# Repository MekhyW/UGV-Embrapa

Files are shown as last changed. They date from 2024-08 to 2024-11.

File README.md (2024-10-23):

# UGV-Embrapa: Unmanned Ground Vehicle for Agricultural Monitoring

Embrapa Logo Insper Logo NASA OSR Logo

## Useful Links

- [Project Documentation](https://mekhyw.github.io/UGV-Embrapa/)
- [First Project Paper (robot platform)](paper-1.pdf)
- [Second Project Paper (autonomous SLAM/navigation module)](paper-2.pdf)
- [Mentor's Projects](https://www.embrapa.br/equipe/-/empregado/351534/thiago-teixeira-santos)
- [NASA JPL Open Source Rover](https://jplopensourcerover.com/)

## What is this project?

This project aims to develop an Unmanned Ground Vehicle (UGV) for monitoring fruit and forestry plots, inspired by NASA's Open Source Rover project. The UGV is designed to navigate autonomously and safely between rows of agricultural fields, providing valuable data for research and management.

## Context

This UGV was developed by students of Insper College as part of their Capstone Engineering Project, in collaboration with Embrapa (Brazilian Agricultural Research Corporation), during the first and second semesters of 2024. The project builds upon the foundation laid by the NASA JPL Open Source Rover, adapting it for agricultural applications.

## Directory Structure

```
UGV-Embrapa/
├── .github/
│   └── workflows/
├── docs/
├── Electronics/
├── Mechanics/
├── Software/
├── README.md
└── ugv-embrapa.pdf
```

## Contributors

- Breno Alencar Araújo
- Bruno Morales Balkins
- Fernando Bichuette Assumpção
- Giulia Carolina Martins de Sampaio
- Felipe Catapano Emrich Melo
- Rafael Eli Katri
- Gabriel Brunoro Motta Tumang
- Luana de Matos Sorpreso

Advisor: Prof. Dr. Vinícius Licks
Mentor: Thiago Teixeira Santos

For detailed information about the project, including setup instructions, technical details, and results, please refer to the [project documentation](https://mekhyw.github.io/UGV-Embrapa/).

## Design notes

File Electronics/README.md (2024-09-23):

# Electronics 

## Schematics and General Operation Details 

The prototype's electronics are composed of two boards: the motor drive board (Motor Board), where the power circuits are located, and the board responsible for controlling the entire system's operation (Brain Board), where the control circuits are located and a Raspberry Pi 4, model B, 8 GB, with a 64-bit quad-core ARM-Cortex A72 microprocessor, running at 1.5 GHz, is located.



### Power Supply Diagrams

First, analyzing the system power supply, a battery supplying 14.8V DC is connected directly to the drive board, passing through a protection circuit, which has a fuse, a 1 kΩ resistor and a diode, which act as protection for the motor circuit. In addition, a voltage and current monitoring module (INA260) is used to measure overcurrent, in addition to a multimeter, which is used for user monitoring of current and voltage data.



The 14.8V voltage is used to power two regulators, a 12V step-down regulator (D24V22Fx), used to power the Roboclaw drivers, and a 5V regulator (D24V150Fx). There is also a third voltage regulator that converts the voltage from 5V to 3.3V (MIC2937A-3.3WT), powering the PWM expansion module (PCA9685), the voltage and current monitor, and the signaling LEDs on both boards. The 5V voltage, in turn, also powers the PWM expansion module, the servos, the Raspberry Pi, the HMI display, and the motor encoders. The motors are powered by Roboclaw via PWM with a maximum voltage of 12V.

### Signal Diagrams

For the system signal diagram, note that a new block has been added, the set between the operator and the radio control, responsible for sending commands via radio waves to the Raspberry Pi, which receives the signal via a USB module. The data received by the microprocessor is sent via serial and used to control the motors and servos.



The control loop for the six motors is controlled by the Raspberry Pi, which receives the reference from the radio control and sends the commands to the Roboclaw drivers, which perform the activation via PWM. The loop is closed by the encoders, which are responsible for the sensing, sending the collected data to the controller present in the driver.

The four servos, in turn, are controlled in an open loop (internally closed) activated by means of a PWM signal. This signal is provided by the PCA9685 module (expansion), used to increase the number of servos that can be controlled, by generating 16 new PWM channels. Communication between this module and the Raspberry Pi occurs via the I2C communication protocol.

Considering the communication between the microcomputer and the voltage and current monitoring module (INA260), it is noted that data is also sent via an I2C communication protocol. The module also communicates with the signaling LEDs to alert the user if its internal shunt resistor detects any change in the power supply system.

In addition to the expansion module and the monitor, communication with the HMI display, which will be implemented in the future, will also occur according to the I2C protocol. The reason for this choice is that the control board has an available I2C bus, which could be adapted for connecting the display with a low number of necessary adaptations.

Another important observation regarding the diagram is that the Raspberry Pi is also responsible for controlling the 12V voltage regulator through an enable signal, turning the 12V output on or off.

A closer look at the control board reveals the presence of some signaling LEDs. These components are intended for communication with the user, signaling, for example, when data is being transferred via the serial port, lighting up when the bits are transferred.

Finally, the last data stream to be analyzed is the emergency status indicator, in which a high logic level digital signal is sent by the emergency button to the microprocessor, which communicates the situation to the user via the HMI display.

## Physical Emergency Circuit

The schematic of the physical emergency circuit used to de-energize the robot is illustrated below.



To indicate the emergency status to the user, a red indicator light was adopted, which lights up as soon as the button is pressed. The component has an internal resistance of 1800 Ω, supporting voltages of up to 24V and is activated by a normally open switch, responsible for closing the circuit after the button is pressed.

A remote emergency button was also implemented, whose operation is explained in the programming folder.

## Display Circuit Details

The schematic of the display pin connection to ensure I2C communication is shown below. The pins for connecting 5V and GND are available on the Raspberry Pi and an extension of the SCL and SDA pins can be found on the control board.



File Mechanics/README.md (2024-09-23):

# Mechanics

## 3D Model
The base 3D model can be found in [OnShape](https://cad.onshape.com/documents/e4f00b1a3d2edb1a84bbba1c/w/8ab8f394324bcc586236ef5d/e/9191e5ad2a70f387b419bc55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) or in the STEP file provided above.



## Adaptations to Official Documentation
Some adaptations were necessary in the assembly of the official documentation, since the components were imported and some of them were not available for delivery. To get around this problem, equivalent parts were purchased that would allow adaptation for the proposed application.
The parts that underwent this adaptation process are listed and commented below.
### Suspension Profiles
The first parts to be adapted were the aluminum profiles that make up part of the robot's suspension, since it was not possible to find them in the lengths specified in NASA's official documentation, 96 mm. As an alternative, larger profiles were purchased and cut to the correct size.



After cutting the profiles, the thread for the M4 screw used in the assembly had to be redone for all four holes in each of the cut parts. The threading operation was carried out manually and consisted of three stages, using taps of different sizes until the desired thread size was reached. The part did not need to be drilled again, since its holes were through holes, covering the entire structure, regardless of length.



### Aluminum Body Bars

The aluminum bars used to assemble the robot body also needed to be adapted, since they were also purchased in a length greater than that specified and then cut to the correct size, 96 mm.

After performing the cutting operations on the parts, it was necessary to drill the bars, since the existing hole was not through like in the profile. In addition, it was also necessary to perform the threading in two stages, as was the case with the other part mentioned above.

During the drilling operation, the following steps were performed to ensure better alignment of the hole:

1. Painting the face to be drilled with a marker.

2. Removing the paint to mark the hole with the aid of a vertical height marker. The line was drawn with a dimension equivalent to half the side of the face, ensuring that the straight lines intersect in the center.

3. Making a central mark to ensure that the drill is not inserted misaligned, a step performed with a center punch, a vice and a hammer.

4. Drilling with the aid of a manual benchtop milling machine, aiming to align the tip of the drill with the marking made in the previous step. Advance and retreat the drill during the process, ensuring chip evacuation and dissipation of the heat generated.



The threading process was also necessary and was redone in a manner identical to the procedure described for the profiles.

The part with the bearing for fitting the suspension was also not available in the original model in NASA documentation, so another with an equivalent internal diameter was used (Figure 28). Although the replacement did not fit perfectly and caused slight structural deformation, it was decided not to make any adaptations because the components could be damaged and there were no substitutes. The resulting deformation effect did not compromise the rover's operation.



## Review of Official Documentation Errors

One of the suspension components was incorrectly identified in the official documentation, with initial code 1601, which in reality corresponds to component number 1611. In the 3D view of the assembly, the part identified with the code corresponding to that informed in the official documentation has an internal diameter with a value of less than 8 mm, not assembling on the specified axle.



## Additional Components Manufactured

To ensure the robot's adaptability to the monitoring environment, some additional components needed to be manufactured, including the camera and LiDAR supports, allowing these components to be placed in the structure in the future.

### Camera Support

As requested by the client, some supports for cameras and a LIDAR were also developed, using Fusion 360 software for modeling and 3D printing technology to materialize the project.

suporte1

Screenshot at Jun 10 11-16-50

### LiDAR Support

suporte3

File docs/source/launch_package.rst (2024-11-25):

Launch Package
===============

The osr_autonomous package contains the launch files for the robot, for operation using the SLAM and navigation stack described in previous sections (for the Raspberry Pi's launch package, refer to the Raspberry Pi's environment setup section).

Usage
-----

1) First, make sure the package is built and sourced in your ROS 2 workspace:

   .. code-block:: bash

      cd UGV-Embrapa/Software/osr_autonomous
      colcon build --packages-select osr_autonomous
      source install/setup.bash

   .. note::
      You can also source the ROS 2 environment from the Environment Setup - Dell Optiplex section. Refer to it for more information.

2) Then you can launch any of the files using the ros2 launch command with the package name and launch file name:

   .. code-block:: bash

      ros2 launch osr_autonomous gps_launch.py

      ros2 launch osr_autonomous ir_depth_launch.py

      ros2 launch osr_autonomous rosbag_launch.py

      ros2 launch osr_autonomous rtab_imu_launch.py

      ros2 launch osr_autonomous stereo_launch.py

3) For the rosbag_launch.py, you can specify a custom directory for saving the bag files:

   .. code-block:: bash

      ros2 launch osr_autonomous rosbag_launch.py bag_dir:=/path/to/save/bags

   .. note::

      Also, ensure that:

      - Your RealSense D435i camera is properly connected
      - If using GPS features, your GPS device is connected and configured
      - The robot's URDF is properly set up in the osr_gazebo package
      - Parameter files exist in the correct locations:
         - ``osr_autonomous/realsense_params/params.yaml``
         - ``osr_autonomous/nav2_params/params.yaml``
         - ``osr_autonomous/nav2_params/map.yaml``

Configuration Notes
--------------------

   - All launch files support parameter overrides via command line arguments
   - RTAB-Map parameters are optimized for real-time performance
   - Transform configurations assume standard sensor mounting positions
   - Nav2 parameters and maps are loaded from the osr_autonomous package

Launch Files
------------

The launch files are designed to support different operational modes and sensor configurations for the UGV. Each launch file serves a specific purpose in the robot's operation, from basic visual SLAM to full GPS-aided navigation.

gps_launch.py
^^^^^^^^^^^^^

This launch file implements a complete navigation stack with GPS integration. It's ideal for outdoor operations where GPS signals are available.

Key Features:

   - Initializes RealSense D435i camera in IR/depth mode
   - Enables IMU (gyroscope and accelerometer)
   - Sets up RTAB-Map for visual SLAM
   - Configures Nav2 for autonomous navigation
   - Integrates GPS data via the NMEA driver
   - Uses robot_localization for sensor fusion
   - Includes GPS waypoint following capability

ir_depth_launch.py
^^^^^^^^^^^^^^^^^^

A simplified version focused on indoor navigation using IR and depth data from the RealSense camera.

Key Features:

   - Configures RealSense D435i for IR and depth streaming
   - Sets up RTAB-Map for visual SLAM
   - Enables Nav2 for autonomous navigation
   - Uses IMU data for improved odometry
   - Excludes GPS-related components

rosbag_launch.py
^^^^^^^^^^^^^^^^

Similar to gps_launch.py but includes ROS bag recording functionality for data collection and post-processing.

Key Features:

   - Includes all functionality from gps_launch.py
   - Adds automatic ROS bag recording of all topics
   - Configurable output directory for recorded bags
   - Useful for development and debugging

lidar_launch.py
^^^^^^^^^^^^^^^

Similar to gps_launch.py but with LiDAR integration for improved mapping and navigation (complete stack without bag recording).

Key Features:

   - Includes all functionality from gps_launch.py
   - Adds LiDAR data integration
   - Improved mapping and navigation capabilities
   - No ROS bag recording

rtab_imu_launch.py
^^^^^^^^^^^^^^^^^^

Specialized configuration focusing on RGB-D SLAM with heavy IMU integration.

Key Features:

   - Uses RGB color stream instead of IR
   - Enhanced IMU integration with RTAB-Map
   - Configured for improved 3D mapping
   - Forces 2D constraints for better ground robot operation
   - More aggressive feature detection settings

stereo_launch.py
^^^^^^^^^^^^^^^^^

Basic stereo vision configuration using the RealSense camera's IR sensors.

Key Features:

   - Minimal configuration using IR and depth
   - No IMU integration
   - Basic RTAB-Map configuration
   - Lighter weight than other launches
   - No navigation stack integration

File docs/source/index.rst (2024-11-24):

.. UGV Embrapa documentation master file, created by
   sphinx-quickstart on Tue Oct 15 21:59:05 2024.
   You can adapt this file completely to your liking, but it should at least
   contain the root `toctree` directive.

UGV-Embrapa: Unmanned Ground Vehicle for Agricultural Monitoring
================================================================

Welcome to the documentation for the UGV-Embrapa project, an Unmanned Ground Vehicle (UGV) for monitoring fruit and forestry plots. 
Here you will find information about the project, how to assemble and use the robot and how to setup the software stack to perform autonomous navigation, mapping and telemetry.

.. toctree::
   :maxdepth: 2
   :caption: Contents:

   papers
   overview
   mechanical_assembly
   schematics_and_wiring
   environment_setup_rpi
   remote_control
   environment_setup_optiplex
   launch_package
   waypoint_navigation
   cloud_architecture
   contributors

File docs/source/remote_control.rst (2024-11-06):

Remote Control Operation
========================

The UGV (Unmanned Ground Vehicle) can be operated manually using a Spektrum DXS radio control transmitter, which communicates with a receiver installed in the UGV. This section describes how to use the remote control for manual operation of the robot.

Controller Setup
----------------

The mapping of control buttons and levers has been configured to facilitate the operation of the UGV. The following parameters have been set for the controller:

- **scale_linear.x**: 0.12
- **axis_linear.x**: 1
- **axis_angular.yaw**: 2
- **axis_angular.pitch**: 4
- **scale_angular.yaw**: 1.25
- **scale_angular.pitch**: 0.25
- **scale_angular_turbo.yaw**: 0.0
- **scale_linear_turbo.x**: 0.0
- **enable_button**: 0
- **enable_turbo_button**: 1

These parameters are used by the ROS 2 `joy` node to interpret the controller inputs.

Control Mapping
---------------

1. **Speed Control**:
   The left lever controls the speed of the UGV. Push forward to move the UGV forward, and pull back to reverse.

2. **Direction Control**:
   The right lever is responsible for steering the UGV. Move the lever left or right to rotate the UGV in the respective direction.

3. **On/Off Switch**:
   The lower central button turns the UGV on or off.

4. **Emergency Stop**:
   The emergency button is located at the top left of the controller. When pressed, it immediately stops the UGV by setting `scale_linear_turbo` to 0.0.

5. **Fine Rotation**:
   A switch at the top right of the controller allows for fine adjustment of rotation.

6. **Deadman Switch**:
   Located on the back of the controller, this button must be continuously pressed to keep the UGV operational. Releasing it will immediately stop the UGV as a safety measure.

Emergency Routine
-----------------

An emergency routine has been implemented to ensure the operational safety of the rover:

1. When the emergency button is pressed, `scale_linear_turbo` is set to 0.0.
2. This results in the rover coming to a complete and immediate stop.

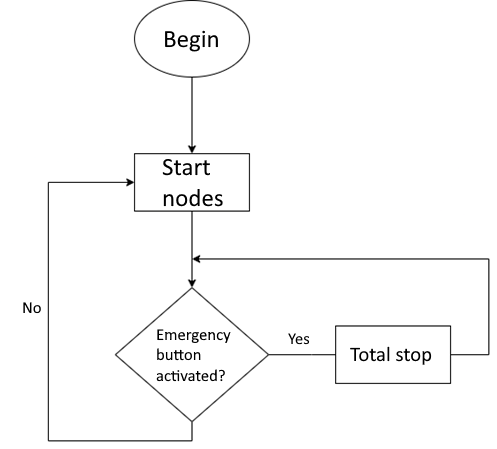
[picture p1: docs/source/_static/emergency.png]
Emergency flowchart


Operating the UGV
-----------------

1. Ensure the receiver dongle is properly connected to the UGV.
2. Turn on the Spektrum DXS radio control transmitter.
3. Use the On/Off switch to power up the UGV.
4. Press and hold the Deadman switch on the back of the controller.
5. Use the left lever to control speed and the right lever to steer.
6. For fine rotations, use the rotation switch at the top right.
7. In case of emergency, press the emergency stop button to immediately halt the UGV.
8. When finished, use the On/Off switch to power down the UGV.

.. note::
   Remember to always operate the UGV in a safe environment and follow all safety protocols.

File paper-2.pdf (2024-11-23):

Veículo Terrestre Autônomo para Monitoramento de Talhões de Silvicultura e Plantações de Frutas

Felipe Catapano Emrich Melo Gabriel Brunoro Motta Tumang Luana de Matos Sorpreso
Rafael Eli Katri

Trabalho de Conclusão de Curso

Relatório do Projeto Final - Capstone

São Paulo - SP – Brasil
Agosto 2024

Felipe Catapano Emrich Melo Gabriel Brunoro Motta Tumang Luana de Matos Sorpreso
Rafael Eli Katri

Veículo Terrestre Autônomo para Monitoramento de Talhões de Silvicultura e Plantações de Frutas

Trabalho de Conclusão de Curso

Relatório do Projeto Final - Capstone

Relatório apresentado aos respectivos cursos de Graduação em

Engenharia | (Computação/Mecânica/Mecatrônica), | como

requisito parcial para a obtenção do título de Bacharel no

respectivo curso.

Professor Orientador: Prof. Dr. Vinicius Licks

Mentor: Thiago Teixeira Santos

Coordenador TCC/Capstone: Prof. Dr. Luciano Pereira Soares

São Paulo - SP – Brasil
Agosto 2024

Felipe Catapano Emrich Melo Gabriel Brunoro Motta Tumang Luana de Matos Sorpreso
Rafael Eli Katri

Veículo Terrestre Autônomo para Monitoramento de Talhões de Silvicultura e Plantações de Frutas

Relatório apresentado aos respectivos cursos de Graduação em

Engenharia | (Computação/Mecânica/Mecatrônica), | como

requisito parcial para a obtenção do título de Bacharel no

respectivo curso.

Professor Orientador: Prof. Dr. Vinicius Licks

Banca Examinadora

Prof. Dr. Vinicius Licks

Insper

Prof. Dr. Fabio Ferraz Junior

Insper

Prof. Dr. Fabricio Jailson Barth

Insper

Prof. Me. Fabio Roberto de Miranda

Insper

RESUMO

Este projeto visa desenvolver um sistema de navegação autônoma para um robô de

monitoramento de silvicultura e pomares montado pela iteração anterior deste Capstone. O

projeto tem como propósito automatizar o processo de monitoramento de tais plantações,

possibilitando a otimização da mão de obra humana. O programa para esta funcionalidade nova

será desenvolvido utilizando o framework ROS 2, e mais especificamente o pacote de

navegação NAV 2. Para conseguir atingir o objetivo final, foi estudado pelo grupo múltiplas

soluções e algoritmos de SLAM (Simultaneous Localization and Mapping) compatíveis com

fusão de sensores de múltiplos tipos, para mapeamento multissensorial robusto em ambientes

não estruturados com terreno irregular. Para achar a solução ideal para os requisitos de projeto,

foi adotado a ferramenta da matriz de soluções.

Palavras-chave: Navegação Autônoma; Monitoramento de plantações; SLAM; ROS 2; NAV

2; UGV;

ABSTRACT

This project aims to develop an autonomous navigation system for a forestry and orchard

monitoring robot assembled by the previous iteration of this Capstone. The project aims to

automate the monitoring process of such plantations, enabling the optimization of human

labor. The program for this new functionality will be developed using the ROS 2 framework,

and more specifically the NAV 2 navigation package. To achieve the final objective, the

group studied multiple solutions and SLAM algorithms compatible with sensor fusion of

multiple types, for robust multisensory mapping in unstructured environments with uneven

terrain. To find the ideal solution for the project requirements, the solution matrix tool was

adopted.

Keywords: Autonomous Navigation; Plantation Monitoring; SLAM; ROS 2; NAV 2; UGV.

3.4 | ESCOLHA DE SISTEMA OPERACIONAL E DISTRIBUIÇÃO DE ROS PARA O MÓDULO DE NAVEGAÇÃO ..... 35

### 1 Introdução

1.1 Proposta do projeto

O objetivo do projeto é a implementação de um sistema de navegação autônoma e de

monitoramento de trajetória para um UGV (Unmanned Ground Vehicle), ou seja, um veículo

terrestre não tripulado. O veículo deve ser capaz de planejar seu movimento e enviar

informações de posicionamento enquanto navega por corredores de talhões, a unidade básica

de plantio agrícola. A iteração atual faz parte de um contexto maior de projetos de UGV’s para

uso agrícola, representando continuidade ao Capstone anterior responsável pela montagem do robô a ser utilizado, capaz de atuar em pomares e talhões de silvicultura (ARAÚJO et al, 2024).

Diferentemente da iteração passada, o UGV não é operado manualmente com um

controle remoto. O robô deverá, com o auxílio de uma ferramenta de software interativa,

receber um conjunto de pontos chamados de waypoints e, sem comandos adicionais do

operador, ser capaz de navegar de ponto a ponto autonomamente. Para isso, foi desenvolvido

um módulo separado de navegação autônoma, composto por um conjunto de sensores e uma

unidade computacional dedicada, que deverá processar tarefas de localização, mapeamento e

navegação e se comunicar com o serviço de atuação dos motores do módulo base do UGV. Isso

se deve principalmente pelo caráter crítico da atuação dos motores do veículo, que não deve ser

comprometido pelos processos alto nível da navegação autônoma.

A navegação autônoma e o acompanhamento do percurso via interface interativa

servirão de base para aplicar futuramente técnicas de agricultura de precisão, principalmente

no que se trata de monitoramento de plantio. Esse caso de uso traz valor para o agronegócio

dado que pode ser usado para controle de pragas e planejamento de plantações. Esse tipo de

monitoramento poderá ser explorado em futuras iterações, que beneficiam da navegação do

robô pelos talhões e a publicação de informações de telemetria que informam o seu

posicionamento.

O UGV, desde a iteração anterior, utiliza o ROS (Robot Operatintg System), um

framework open-source de robótica que padroniza o desenvolvimento de robôs e facilita a

colaboração entre usuários. Nesse sentido, o ROS oferece padrões de comunicação entre

sensores, atuadores e computadores, permitindo que o desenvolvedor não se preocupe com a

implementação baixo nível da transmissão de dados. Além disso, o ROS disponibiliza

ferramentas de visualização e definição de waypoints.

O framework permite que projetos sejam convertidos em pacotes que podem ser

facilmente instalados e acessados por outros desenvolvedores. Desse modo, a comunidade ROS

de robótica mantém pacotes open-source sobre as mais diversas áreas de atuação no campo de

robótica. ROS também é relevante para aplicações no mercado de trabalho, sendo que mais de

900 empresas o utilizaram em 2023, com um aumento de 22.9% em relação ao ano anterior

(SCOTT, 2024).

No que diz respeito a navegação, os pacotes ROS utilizados fazem parte da plataforma

NAV 2. Esses pacotes são desenvolvidos pela Open Navigation, uma empresa que cria soluções

open-source para tarefas de navegação. O NAV 2 é uma plataforma utilizada no mercado, sendo

usada por empresas como Toyota, LG e Bosch (NAV 2, 2024). Um grande diferencial da

plataforma é sua modularidade, sendo que é fácil customizar o comportamento de seus

planejadores, ou até mesmo criar comportamentos usando o sistema de plugins (DOCS NAV

2, 2024). Outro ponto forte é a disponibilidade de plugins prontos com algoritmos de

planejamento e suavização de rotas, árvores de comportamento, entre outros (DOCS NAV 2,

2024).

Um sistema de navegação autônoma depende de técnicas de localização e mapeamento

para obter informações do posicionamento do robô em relação a um ponto de referência (Corke,

2011, p. 125). Uma solução para isso é uso de GPS (Global Positioning System), um sistema

que estima a posição diretamente com uso de satélites. Sensores GPS-RTK são comumente

usados, oferecendo precisão na escala de centímetros. Entretanto, para o caso de uso do projeto,

no contexto da silvicultura com áreas densas de árvores, é conhecido que essas áreas sofrem de

bloqueios e reflexões de sinal (AGUIAR et al, 2020), o que gera instabilidades.

Nesse sentido, uma técnica relevante é o SLAM (Simultaneous Localization and

Mapping), que consiste na localização e mapeamento simultâneos de um ambiente não

explorado (CORKE, 2011, p. 167). Existem diversas implementações de SLAM, incluindo

SLAM baseado em LiDAR’s 3D e SLAM visual que são relevantes para ambientes externos

(FASIOLO et al, 2023). Outra questão relevante é o SLAM multi-sensor, que realiza fusão de

sensores para evitar o acúmulo de erros na coleta dos sensores, também chamado de drift

(FASIOLO et al, 2023). Isso é relevante em ambientes externos, que são sujeitos a efeitos

climáticos desfavoráveis, uma vez que as leituras de um sensor podem compensar falhas do

outro (ZHU, 2024).

Soluções de SLAM usando LiDAR 2D são conhecidas, computacionalmente eficientes

e robustas para ambientes fechados, entretanto elas não têm a mesma eficácia no contexto do

projeto como fonte única de sensoriamento (REGER, 2022) e podem assumir um papel auxiliar

na fusão de sensores. Esse auxílio pode se dar tanto no refinamento da odometria visual, quanto na otimização do mapa com a identificação de loop closures (LABBÉ, 2019).

Com essas questões em mente, propõe-se utilizar uma câmera de profundidade Intel

Realsense D435i e um LiDAR 2D Robotis LDS-02 para as tarefas de localização e

mapeamento, em conjunto com o módulo de GPS. Será utilizado o pacote ROS RTAB-MAP,

um projeto open-source da Université de Sherbrooke, que se diferencia por oferecer suporte a

uma variedade de sensores e pela possibilidade de realizar SLAM multi-sensor. A câmera

Realsense será utilizada para extrair odometria visual e coletar features usando o modo RGB-

D e o IMU interno da câmera será usado como referência para aperfeiçoar o SLAM. O LiDAR

2D também será utilizado no refinamento da odometria visual e na otimização do mapa com a

identificação de loop closures.

1.2 Origem do Desafio

Com base no relatório final do semestre passado foi pensado na origem do desafio,

considerando que o resultado de ambos os projetos é o mesmo. A Embrapa (Empresa Brasileira

de Pesquisa Agropecuária) é uma empresa que foca em pesquisa para a agropecuária no Brasil.

Se trata de uma empresa pública vinculada ao Ministério da Agricultura e Pecuária (MAPA),

criada em 1973.

O objetivo do desenvolvimento do UGV no contexto agrícola é facilitar o

monitoramento de talhões de fruticultura e silvicultura, permitindo que esse trabalho se torne

mais preciso e rápido. O talhão é uma parte do solo que representa a unidade mínima de cultivo.

A separação por talhões é de extrema relevância para a fruticultura pois permite um

controle por área da fruta, dessa forma, é possível isolar um talhão que esteja contaminado por

pragas, por exemplo. Além disso, cada talhão pode conter um tipo de fruta específico, o que faz

com que seja possível uma maior organização no plantio e na colheita.Já no caso da silvicultura,

o talhão também se mostra muito importante, uma vez que, a área florestal é dividida em

unidades territoriais de acordo com características específicas da floresta, assim cada talhão

tem o seu método silvicultural adequado.

Dessa forma, é evidente que o monitoramento dos talhões é essencial para o controle de

pragas e o planejamento de toda a produção e colheita. Por conta da grande relevância do setor agrícola no Brasil, o monitoramento de talhões realizado por seres humanos pode ser dificultado

por conta do grande número de talhões ou até mesmo sua extensão, dessa forma, a inclusão de

UGVs nessa etapa do processo produtivo pode ser de grande auxílio para a realização dessa

tarefa, além de permitir que haja um planejamento maior sobre aquela área.

Atualmente, existem algumas maneiras distintas de realizar o monitoramento, nenhuma

delas tão automatizada quando o UGV. No caso do monitoramento de pragas do mamão em

2018, foi feito um aplicativo móvel onde o produtor preenche planilhas com informações

relevantes como insetos encontrados e quantidade de frutos. Com isso o aplicativo pode

recomendar a pulverização da plantação, além das informações em tempo real disponibilizadas

pelo aplicativo (RODRIGUES et al, 2018).

Essa tecnología, apesar de ainda se mostrar menos automatizada que o UGV, onde não é

necessário que um operador preencha uma planilha, já que o robô já analisa os dados por conta

própria, já apresenta uma grande evolução em comparação com alguns anos antes. Em 2009, o

controle das pragas da Lima ácida Tahiti, que apesar de ser uma fruta distinta é suficiente para

comparação das tecnologías, era realizado de maneira completamente manual. O inspetor de

pragas era o trabalhador cuja função era detectar as pragas utilizando materiais como lupa de

bolso, canivetes, tesoura, fitas, etc e registrar para levar as informações a um outro profissional.

O manejador de pragas, por sua vez, era o responsável por analisar a situação e determinar uma

ação a ser tomada. (SANTOS FILHO et al, 2009)

Com isso, é possível concluir que a tecnología de monitoramento de plantações está

evoluindo rapidamente e o UGV seria a próxima etapa desta evolução, tornando o processo

cada vez mais rápido e eficaz.

1.3 Escopo do projeto

Este projeto tem como principal objetivo transformar o robô montado pela equipe

anterior em um UGV capaz de seguir waypoints evitando colisões com obstáculos. Também

será disponibilizado alguma forma de monitoramento em tempo real da posição e orientação

do robô seguindo algum critério de localização, assim como possíveis mensagens de status.

Além disso, o projeto pressupõe a ocorrência de futuras iterações executadas por outras

equipes. Portanto, o escopo inclui a documentação de tudo que foi produzido, a fim de tornar o

projeto facilmente reproduzível e continuável.

1.4 Mapeamento dos stakeholders

Os stakeholders do projeto são constituídos por alunos do Insper selecionados pelo

programa Capstone, o professor orientador responsável pela equipe, e um representante da

Embrapa que serve como mentor e o ponto de contato entre a equipe do Insper e a empresa.

A seguir, está descrito visualmente as funções e posições de cada stakeholder.

Tabela 1 - mapeamento dos stakeholders (autoria própria)

1.5 Questões Éticas e Profissionais

Para esse projeto, foram levadas em consideração questões éticas e profissionais e seus

impactos ambientais econômicos e sociais. Essas questões éticas e profissionais foram pensadas

com base no relatório final do semestre passado.

Um dos principais impactos sociais da utilização de UGVs na agricultura é a

substituição dos trabalhadores por conta da automação de um trabalho antes realizado pelo

homem, assim, muitos empregos podem ser perdidos por conta dessa nova tecnologia. Levar

isso em consideração é relevante como forma de prever os impactos dessa implementação e

com isso planejar ações para reduzir o impacto negativo na vida das pessoas.

Além disso, deve ser levado em conta aspectos ambientais na produção, uso e descarte

dos UGVs. Dessa forma, é necessário estudar aspectos de contaminação de solos, rios, entre

outros, para então poder evitar impactos ambientais tanto na produção desses robôs, quanto no

seu descarte e manutenção.

Outro aspecto importante é na utilização dos UGVs. O principal objetivo deles é coletar

informações e dados dos respectivos talhões, assim, é necessário garantir a segurança e

privacidade desses dados, ou seja, proteger-se contra o mau uso e o vazamento de informações

coletadas pelo robô.

1.6 Normas Técnicas

Neste projeto foram utilizadas as seguintes normas técnicas, desde o planejamento até

a execução.

Uma das normas utilizadas é a IEEE 1872.2-2021. Ela faz parte do instituto IEEE, uma

organização responsável por normas nas diversas áreas da engenharia elétrica e eletrônica

(IEEE, (https://www.ieee.org/about/at-a-glance.html) 2024), e mais especificamente, pertence ao RAS, o setor de robótica e automação

(IEEE-RAS, (https://www.ieee-ras.org/about-ras) 2024). Essa norma padroniza conceitos e definições relevantes para robótica

autônoma, nisso se inclui também padrões de arquitetura para aplicações de navegação

autônoma (IEEE-RAS, (https://standards.ieee.org/ieee/1872.2/7094/) 2022). Esse tipo de norma que apresenta definições de conceitos de uma

área é conhecido como norma ontológica.

Outra norma relevante é a ISO 18646-2:2024. Essa norma pertence a ISO, a organização

internacional de normalização, que tem membros representantes em mais de 170 países (ISO, (https://www.iso.org/about)

2024). Essa norma em específico trata sobre a padronização na navegação de robôs, o que inclui

acurácia em dados de posicionamento, capacidade de desviar de obstáculos, qualidade do

mapeamento, entre outros tópicos (ISO, (https://www.iso.org/standard/82643.html) 2024).

1.7 Recursos

O projeto tem disponibilidade de recursos de hardware e de infraestrutura para ser

executado. Foram priorizados o uso de sensores e computadores disponíveis prontamente em

laboratórios. Isso se deve ao custo considerável que componentes de robótica podem alcançar

e pelo tempo vago no cronograma que o envio pode causar. A seguir segue as informações de

quais recursos foram utilizados.

O UGV utilizado é baseado no Open Source Rover, um projeto de código aberto da

Nasa, que consiste em um robô com custo acessível e de rápida manufatura similar aos modelos

que exploram a superfície de Marte. Esse UGV já foi montado previamente por um grupo do

Capstone Insper do primeiro semestre de 2024, que também modificou o modelo da Nasa para

ter suportes para câmeras e sensor lidar, os quais podem ser utilizados no processo de navegação

autônoma. Portanto, o UGV que será utilizado já está montado e suficientemente pronto para uso. (ARAÚJO et al., 2024, p. 88).

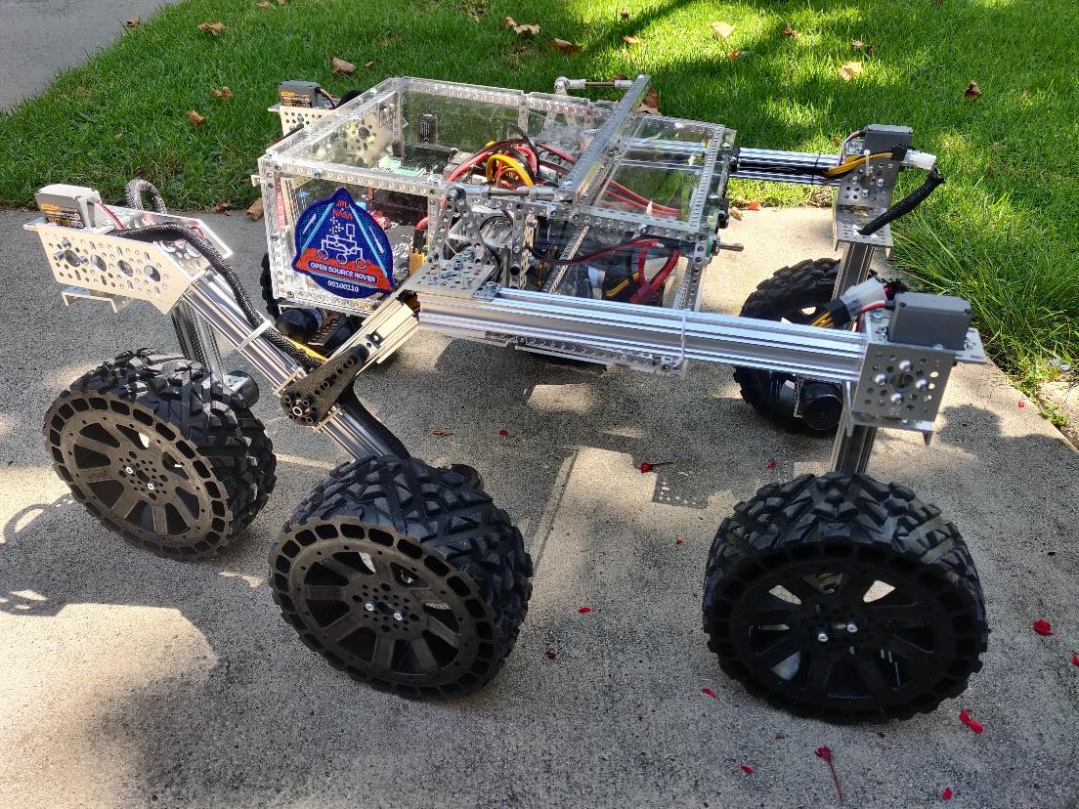
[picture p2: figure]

Figura 1 - Foto do OSR, (JPL OPEN SOURCE ROVER, 2023)

Em termos de infraestrutura, o Insper oferece recursos como os laboratórios, que

permitem acesso a materiais, máquinas e ambientes especializados para o trabalho. Além disso,

especialistas da área, como técnicos e professores, podem ser consultados no andamento do

projeto.

Para a montagem do módulo de navegação autônoma, os recursos necessários foram:

- Computador Dell OptiPlex 7000 MFF
- LiDAR Robotis LDS-02
- Câmera Intel Realsense D435i
- GPS Quectel L80

Em testes prévios, também foram utilizados:

- Kit de desenvolvedor Nvidia Jetson TX2
- Computador Intel NUC D34010WYK

1.8 Revisão do Estado da Arte

O projeto atual está dentro do contexto de navegação autônoma em ambientes agrícolas

e no uso de interfaces humano-robô (HRI) para envio e recebimento de dados. Esses tópicos se relacionam com outras áreas de estudo, como localização e mapeamento, algoritmos de

planejamento de rotas, entre outros.

1.8.1 Aplicações de robótica e monitoramento na agricultura de precisão
Nas últimas décadas, técnicas de SLAM foram extensivamente aprimoradas e

estendidas para várias tarefas dentro da agricultura. Isso é especialmente motivado pelo rápido

desenvolvimento do maquinário agrícola inteligente e proporciona a liberação de parte

significativa da mão de obra em regiões onde há a prática de agricultura. Aplicações nessa área

onde SLAM já foi e ainda é usado de forma significativa incluem, mas não limitadas a

(HAIZHOU et al, 2022):

| • Reconstrução tridimensional de alta fidelidade
| • Detecção e mapeamento de troncos de árvores
| • Previsão de rendimento
| • Monitoramento da altura da cultura e colheita
| • Polinização autônoma
| • Capina de precisão autônoma
| • Controle de pragas

No Brasil, desde 2014, drones e land rovers, como o Agribot e o Mirã, têm sido usados

pela Embrapa para dar suporte ao aumento da precisão na agricultura, por meio da geração de

dados relevantes da plantação e do solo em tempo real. Isso pode ser feito, portanto, por meio

desses mecanismos, dos quais dados de solo e planta podem ser adquiridos diretamente,

contribuindo assim para o gerenciamento eficiente e sustentável da produção agrícola. Tais

mecanismos fazem uso extensivo de técnicas de SLAM e são diretamente beneficiados pelo

seu avanço. (FRANCHINI et al, 2018)

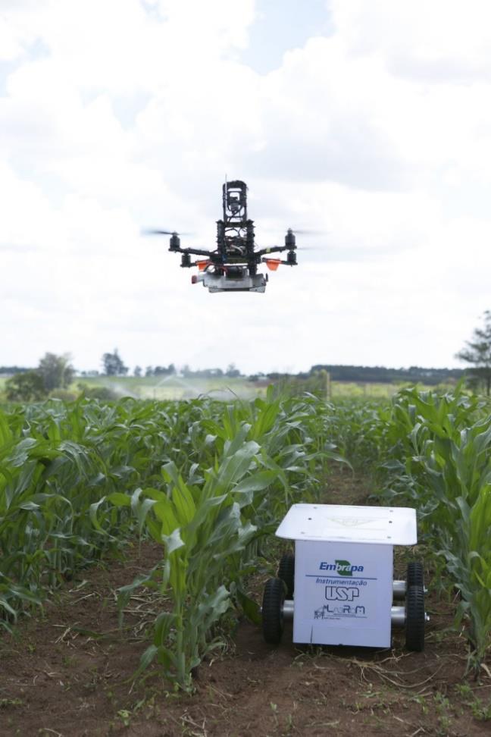
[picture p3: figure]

Figura 2 – Rover experimental e Drone Mirã

As fotografias aéreas de alta resolução capturadas por veículos aéreos autônomos

podem detectar condições de estresse hídrico, pragas e doenças nas plantações, a partir das

quais, por meio de análises específicas, áreas de baixa produtividade pode ser mapeadas.

Mas os Rovers terrestres, como o Agribot, trabalham no nível do solo. Eles percorrem os

campos e detectam doenças e deficiências de nutrientes, que podem ser tratadas por

sensores avançados, como o espectrômetro de luz, capaz de capturar anomalias

impossíveis de serem detectadas pelo olho humano. A união desses veículos proporcionará

uma visão completa da variabilidade espacial nas lavouras, permitindo que os agricultores

realizem seu trabalho com segurança e precisão. Faz parte de uma estratégia da Embrapa

para modernizar e tornar a agricultura brasileira mais competitiva, aproveitando assim as

tecnologias de automação e sensoriamento remoto para garantir a sustentabilidade e a

eficiência do setor. (REVISTA RURAL, 2014)

1.8.2 Sensores para localização no contexto agrícola
Existe uma variedade de sensores que podem ser usados para a obtenção de dados de

localização (HAIZHOU, 2022). A tarefa de localização consiste em relacionar a posição atual do veículo a um sistema de coordenadas, sendo possível utilizar uma abordagem global como

o GNSS, que usa satélites para obter referências de georreferenciamento, ou locais, que usam

sensores para estimar o deslocamento em relação a períodos anteriores (FASIOLO et al, 2023).

Segue a descrição de alguns sensores que são utilizados no estado da arte do cenário agrícola.

Em relação a localização global, um tipo de sensor que tem destaque pela sua precisão

é o Real-Time-Kinematic-GNSS ou RTK-GNSS (FASIOLO et al, 2023). Sensores GNSS

convencionais recebem informações de distanciamento de satélites e as usam diretamente para

estimar a localização, usualmente atingindo precisões na escala de metros. Já sensores RTK-

GNSS utilizam dois receptores para realizar a estimativa, um deles em uma estação fixa e outro

no veículo. Com isso, o receptor da estação consegue ser usado para aumentar a precisão da

estimativa, que costuma estar na escala de centímetros (FASIOLO et al, 2023).

Entretanto, em áreas de agricultura densas, como as do caso de uso do projeto, sensores

GNSS convencionais e RTK sofrem de multi-reflexão e bloqueios de sinal, que afetam

negativamente o uso do sensor (AGUIAR et al, 2020). Outra questão relevante é a fusão de

sensores GNSS com unidades de medição inercial (IMU), que usam a técnica de dead reckoning

para estimar dados de orientação, que usualmente não estão disponíveis para um receptor GNSS

(FASIOLO et al, 2023). Além disso, receptores atuam com uma frequência média

consideravelmente baixa de 1 Hz, enquanto IMU’s tem frequências médias superiores a 1 kHz,

o que torna a fusão entre os dois sensores interessante para preencher lacunas entre os dados de

GNSS (FALSIOLO et al, 2023).

Já em relação a localização local, sensores LiDAR 3D e câmeras de profundidade são

comumente utilizadas. LiDAR’s são sensores que usam como base o tempo de reflexão de um

laser para medir distâncias de seus arredores, sendo que técnicas como ICP podem ser utilizadas

para comparar duas leituras diferentes e estimar o deslocamento entre elas (FASIOLO et al,

2023). Já câmeras de profundidade oferecem dados de imagem e profundidade, podendo ser

baseadas em técnicas stereo ou time of flight.

Para localização visual, é comum o uso de técnicas de extração de features, que são o

conjunto pontos de interesse coletados da imagem (keypoints) e suas informações relevantes

(descriptors), que em seguida são comparados entre os frames para estimar o deslocamento (LABBÉ, 2019).

Por um lado, LiDAR’s são mais robustos em relação a mudanças de iluminação

(FASIOLO et al, 2023), mas são consideravelmente mais caros e podem ser prejudicados por

condições climáticas como chuvas e neblinas (REGER, 2022).

1.8.3 Comparação de implementações de SLAM Open Source
Uma técnica relevante para a navegação autônoma é o uso de SLAM, um método de

mapear os arredores do robô enquanto ele anda, sem informações prévias. O SLAM entra no

contexto de estratégias de localização, e pode ser dividido em tarefas de extração de features

dos dados de sensores para a construção do mapa, o que é conhecido como Front-End, e na

otimização do mapa, conhecido como Back-End (KAZEROUNI et al, 2022). Outra questão

relevante para o SLAM é a identificação de pontos que já foram visitados previamente de modo

a corrigir imperfeições do mapa, o que é conhecido como loop closure (KAZEROUNI et al,

2022).

Para contextualizar, determinados algoritmos de planejamento de rotas como A* ou

Djikstra dependem de mapeamento para serem utilizados. Inclusive, o uso da plataforma padrão

de navegação do ROS, NAV 2, depende de técnicas de mapeamento como o SLAM ou de

AMCL, uma técnica que utiliza um mapa previamente feito.

Tanto o SLAM, quanto algoritmos de planejamento de rotas são técnicas conhecidas e

já possuem diversas implementações desenvolvidas por grupos acadêmicos e distribuídas em

pacotes ROS. Nesse sentido, o propósito do projeto “Comparison of Various SLAM Systems

for Mobile Robot in an Indoor Environment” (FILIPENKO, 2018) é realizar o benchmark de

diversos pacotes conhecidos de SLAM no framework ROS, utilizando uma variedade de

configurações de sensores diferentes.

Em questão de hardware, o robô utilizado pelo projeto usa uma placa Nvidia Jetson

TX1, um LiDAR 2D Hokuyo, uma câmera estérea e uma câmera convencional. Foram testados

pacotes de SLAM baseados em LiDAR 2D e SLAM visual.

Tabela 2 - comparação entre técnicas de SLAM (Filipenko, 2018)

Os pacotes que tiveram os melhores resultados foram RTAB-MAP, ORB-SLAM e

Cartographer. As soluções de LiDAR 2D, como Cartographer, obtiveram os melhores

resultados. Já em relação ao SLAM visual, os pacotes RTAB-MAP e ORB SLAM se

sobressaíram, sendo que o primeiro teve dificuldades em ambientes com paredes

monocromáticas e o último teve dificuldades em calcular a escala das distâncias na imagem

para produzir o mapa.

Vale ressaltar que as condições de teste não são iguais ao da proposta de projeto, dado

que eles foram feitos em ambientes fechados. Isso pode causar um viés na análise de

desempenho, principalmente a favor do uso de LiDAR 2D, uma vez que ambientes abertos não

são favoráveis para uso de LiDAR 2D como fonte única de sensoriamento (REGER, 2022).

O diferencial das soluções de SLAM visual que usam câmeras de profundidade é o

mapeamento em 3D. Além disso, pacotes como o RTAB-MAP oferecem opções de SLAM

multi-sensor e projeção do mapa para o plano 2D, o que é útil para a integração com o pacote

de navegação.

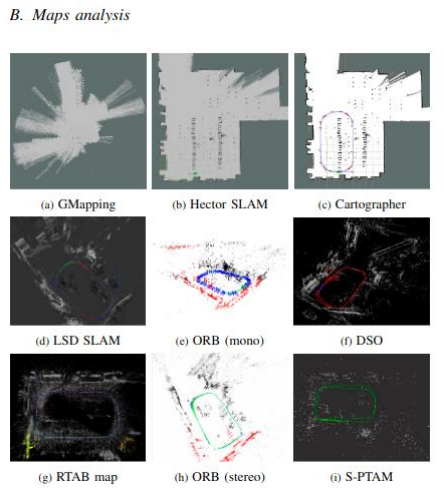
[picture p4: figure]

Figura 3 - visualização dos mapas criados por diferentes métodos de SLAM (Filipenko, 2018)

1.8.4 ROS
Considerando o estado da arte, é importante também ressaltar a adoção do framework

ROS 2 ao invés de sua implementação antecessora. O primeiro ROS, que foi desenvolvido com

foco originalmente em uso acadêmico, causou impacto na indústria devido ao crescimento de

bibliotecas de código aberto, entretanto não possui recursos considerados importantes para

projetos comerciais. Devido a isso, foram iniciados extensivos esforços por parte da

comunidade para a migração de soluções. Desde 2023, o número de downloads de ROS 2

superou o de ROS 1, chegando a 57.88% do total desse ano, o que indica que ele está cada vez

sendo mais adotado pela comunidade de robótica (SCOTT, 2024). Além disso, em relação ao

ano anterior, o número de downloads e pacotes ROS 2 instalados aumentou em 18.05% e

41.44%, respectivamente (SCOTT, 2024).

Melhorias em relação ao projeto original incluem melhoria de qualidade de serviço na

transmissão de mensagens, integração plena entre as diferentes implementações das API’s de linguagens, que agora são convertidas para o padrão RCL feito em C, e a possibilidade de

implementar tarefas em tempo real (ROS 2 DESIGN, 2024).

Uma vez que cada distribuição do ROS está diretamente atrelada a uma distribuição do

sistema operacional Ubuntu Linux, o fim da vida da versão compatível com a última versão

disponibilizada do ROS original (denominada Noetic Ninjemys) implica no encerramento de

suporte oficial a partir de maio de 2025. Parte das migrações observadas, portanto, se deve ao

fato de que a falta de atualizações e recursos de segurança representa um risco severo para

aplicações comerciais, uma vez que se estaria usando pacotes com vulnerabilidades conhecidas.

### 1.8.5 Projetos semelhantes

De modo a entender como estes e outros desafios semelhantes de navegação autônoma

são atendidos, foi realizada uma pesquisa de projetos semelhantes.

A Clearpath Robotics é uma empresa de robótica que atende o segmento de UGV’s de

agricultura. A empresa canadense apresenta robôs especializados para a movimentação em

áreas externas (CLEARPATH ROBOTICS, 2024) e softwares proprietários para a navegação

autônoma em plantios (CLEARPATH ROBOTICS, 2024). A Clearpath também oferece kits

de sensores para adaptar robôs proprietários ou de fora da empresa para o uso de navegação

autônoma. Um diferencial deles é o suporte de sistemas open-source como ROS, que permite

fácil colaboração e integração com outros projetos.

Como o seu principal software de navegação autônoma para ambientes agrícolas,

OutdoorNav, não é open-source, não é possível saber as técnicas de navegação utilizadas. Sabe-

se que a estrutura do problema é semelhante, sendo que o caminho a ser feito é descrito também

com waypoints.

Entretanto, pelos kits de sensores é possível ter noção do que é utilizado em situações

práticas no mercado. A versão padrão do kit, de maior custo e desempenho, acompanha um

sensor LiDAR 3D, GPS RTK de duas antenas e um IMU (CLEARPATH ROBOTICS, 2024).

Já a versão para iniciantes acompanha duas câmeras de profundidade Realsense e um sensor

GPS RTK (CLEARPATH ROBOTICS, 2024). Ambos os kits apresentam uma unidade de

processamento separada do computador principal, sendo que esse possui versões com placas da

série Nvidia Jetson ou computadores Mini ITX (CLEARPATH ROBOTICS, 2024).

Outro projeto relevante é o Rovy (SCHNABEL, 2020), feito por um entusiasta de

robótica que buscava rodar SLAM e navegação autônoma em uma Raspberry PI 4. Para isso,

foi necessário fazer mudanças de otimização de código em diversos pacotes de mapeamento,

navegação e até em firmware de sensores. Dentre esses se encontram o pacote RTAB-MAP,

librealsense e NAV 1. Percebe-se que a tarefa de otimização é complexa, a qual foge do escopo

do projeto atual.

No fim, o projeto teve sucesso em rodar SLAM visual baseado em câmeras de

profundidade simultaneamente com o pacote NAV 1 para o planejamento de rotas. Ele otimiza

o cálculo da odometria visual usando uma câmera Realsense T265, a qual faz os cálculos

internamente sem depender da Raspberry Pi. O projeto também conta com uma Realsense D435

para alimentar os dados de SLAM. O Rovy usa o RTAB-MAP, sendo capaz de gerar mapas em

3D, e usa um planejador de rotas customizado, otimizado para o seu uso (SCHNABEL, 2020).

A análise desse projeto é interessante porque demonstra as limitações do uso de uma

Raspberry Pi 4 para o processamento simultâneo de SLAM, navegação e acionamento de

motores, e o potencial de como contorná-las. Apesar de ser possível, a solução precisa de um

trabalho extenso de otimização.

1.8.6 Algoritmos de planejamento de rota e NAV 2
Existem dois grandes grupos de algoritmos de planejamento de rota, os clássicos e

heurísticos (LOGANATHAN E AHMAD, 2023). Os clássicos, como Djikstra, A*, Voronoi e

Rapidly-exploring Random Tree, são algoritmos menos reativos, pensados para ambientes mais

estáticos e consideravelmente mais exigentes computacionalmente do que os heurísticos. Já os

heurísticos, como Ant Colony Optimization e os baseados e redes neurais e algoritmos

genéticos, tendem a ser soluções mais robustas, sendo alvo de pesquisas no estado da arte

(LOGANATHAN E AHMAD, 2023). Entretanto, os algoritmos heurísticos não estão

disponíveis em frameworks de navegação ROS, sendo que as poucas opções disponíveis são

feitas por entusiastas e pesquisadores e de difícil integração.

Dentro do contexto do NAV 2, existem duas principais etapas de planejamento de rota:

planejadores e controladores. Os planejadores consideram que possuem conhecimento absoluto

do ambiente e são menos reativos a mudanças, assumindo papel de planejador da rota global

até o objetivo (NAV2, 2024). Em contrapartida, os controladores não assumem conhecimento

fora da região do mapa local, sendo reativos a mudanças para evitar colisão com obstáculos e

obedecer a restrições cinemáticas (NAV2, 2024). Na maioria dos casos do NAV 2, controladores não são algoritmos de planejamento de rotas em si, mas sim algoritmos que

alteram as trajetórias montadas pelo planejador.

No framework NAV 2, só existem planejadores baseados em decomposição de células,

sendo eles ou feitos com base em Djikstra ou em A* (NAV2, 2024). Existem também plugins

feitos por entusiastas que utilizam a técnica de Rapidly-exploring Random Tree (RRT)

((MMCZA, 2023).

Já em relação aos controladores, existe uma maior variedade. Controladores como

Regulated Pure Pursuit e Vector Pursuit são baseados em path tracking com suavização em

curvas fechadas (NAV2, 2023). Já o DWB usa técnicas de amostragens e otimizações de

funções de score para equilibrar o contorno de obstáculos e a trajetória global ao objetivo

(NAV2, 2023). Por fim, outro controlador relevante é o Graceful, que tem uma preocupação

com a suavidade da trajetória (NAV2, 2023).

### 2 Metodologia

2.1 Gestão do Projeto

Para o desenvolvimento e gestão do projeto será utilizada a metodologia de PDP de Pahl

& Beitz (Pahl et al, 2005). Tal método define uma sequência lógica de design e produção de

produtos de engenharia. Para auxiliar a equipe durante o desenvolvimento será utilizado a

plataforma Notion que integra ferramentas como Kanban, calendário online e uma linha de

tempo das tarefas.

2.1.1 Metodologia de Pahl & Beitz

A metodologia de Pahl & Beitz define um fluxo de trabalho metódico e iterativo para o

processo de planejamento e execução de um projeto de engenharia. A ferramenta contém 4

grandes fases: investigação, design conceitual, design de materialização e detalhamento. Cada

uma dessas fases elencadas anteriormente agrupa diversas tarefas e resultados esperados,

podendo uma macro fase sobrepor a outra em certos períodos.

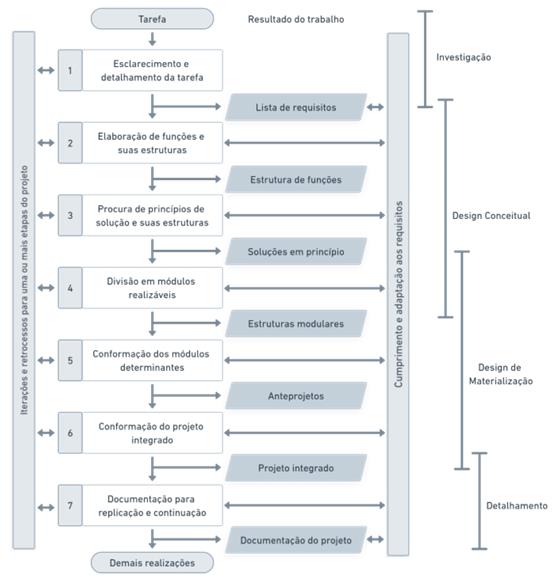
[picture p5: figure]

Figura 4 - Estrutura do método Pahl & Beitz adaptada (Apud Captsone grupo do peixe-robo 2024.1)

2.1.2 Ferramentas de Gestão

Para auxiliar o grupo a manter a organização e acompanhamento das tarefas, assim

como marcar reuniões e guardar documentos, foi utilizada a plataforma Notion. Neste serviço

é possível criar páginas personalizadas que contém múltiplas funcionalidades diferentes, desde

documentação e orientações para usuários, mas também uma ferramenta completa de

acompanhamento de tarefas.

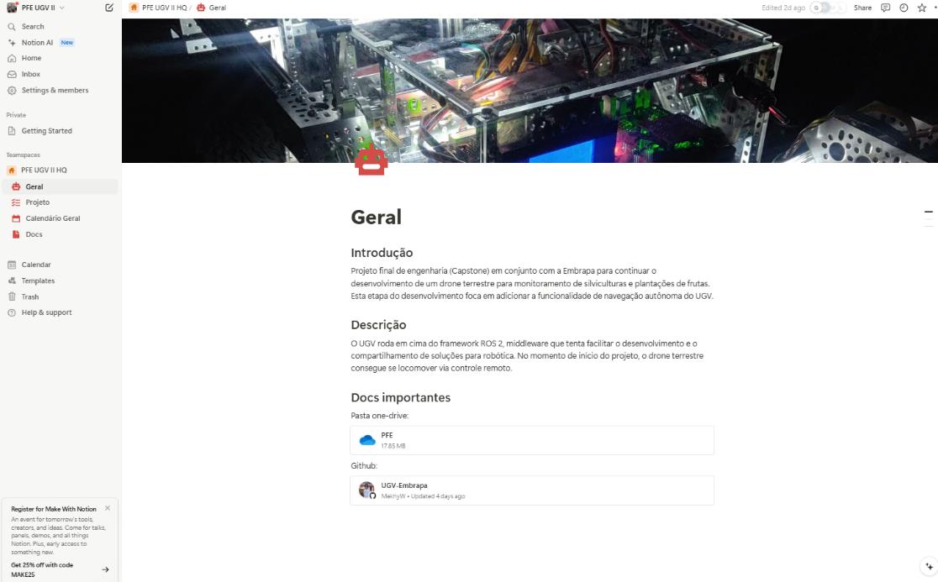
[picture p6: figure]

Figura 5 - landing page do Notion criado pela equipe (autoria própria)

Para este projeto foi criado 4 seções: Geral, Projeto, Calendário Geral e Docs. O Geral

contempla uma breve explicação do projeto, assim como um meio de acesso rápido a outras

ferramentas mais específicas utilizado pela equipe. Dentro de Projeto está configurada uma

página completa para acompanhamento do projeto, contendo uma lista de todas as tarefas, um

Kanban e uma linha de tempo (cronograma) que dá para ser visualizada de múltiplas formas

utilizando filtros diferentes. Por fim, o Calendário Geral é utilizado para manter um controle

sobre reuniões marcadas e eventos relacionados ao projeto, e o Docs é uma página dedicada

para associar possíveis tarefas a documentos específicos delas.

2.2 Análise de Riscos

A análise de riscos é feita com base no capítulo 11 do guia PMBOK. Os riscos do projeto

são analisados em duas dimensões, a probabilidade de ocorrência e a sua gravidade, ou seja, as

consequências caso ele realmente ocorra. Os riscos podem ser classificados como técnicos,

organizacionais, externos ou de gestão de projetos. Uma vez listados os riscos, ele recebe um

índice de probabilidade de ocorrência e um índice de gravidade para o escopo do projeto,

qualidade, cronograma e custo. Assim, o maior dos índices de gravidade é multiplicado pelo

índice de probabilidade para determinar a prioridade do risco com relação aos demais, ou seja,

aquele que tiver um maior valor resultado dessa multiplicação, é o risco com maior prioridade.

Além disso, são pensadas em ações preventivas para cada um deles. Na tabela a seguir o que

está marcado em vermelho representa um risco maior e em amarelo um risco moderado.

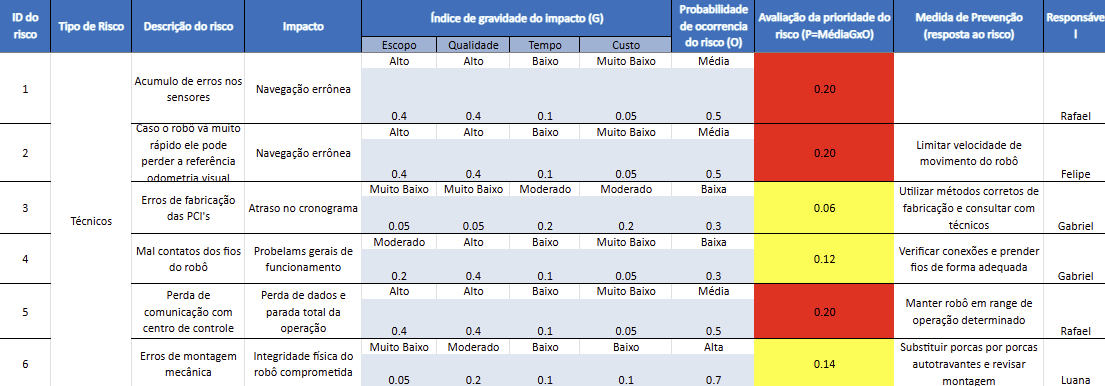
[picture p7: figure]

Figura 6 - Tabela de riscos técnicos (autoria própria)

Figura 7 - Tabela de riscos organizacionais, de gestão de projetos e externos (autoria própria)

2.3 WBS e Cronograma

Para organização de tarefas e prazos o grupo elaborou um WBS e com isso um

cronograma. O WBS tem como sua entrega final a navegação autônoma do UGV, tendo sido

dividido em 6 entregáveis. O Desenvolvimento foi dividido com 2 níveis de detalhe, sendo o

primeiro composto por uma divisão mais geral entre software, eletrônica e mecânica, tendo

cada uma dessas divisões seus pacotes de trabalho.

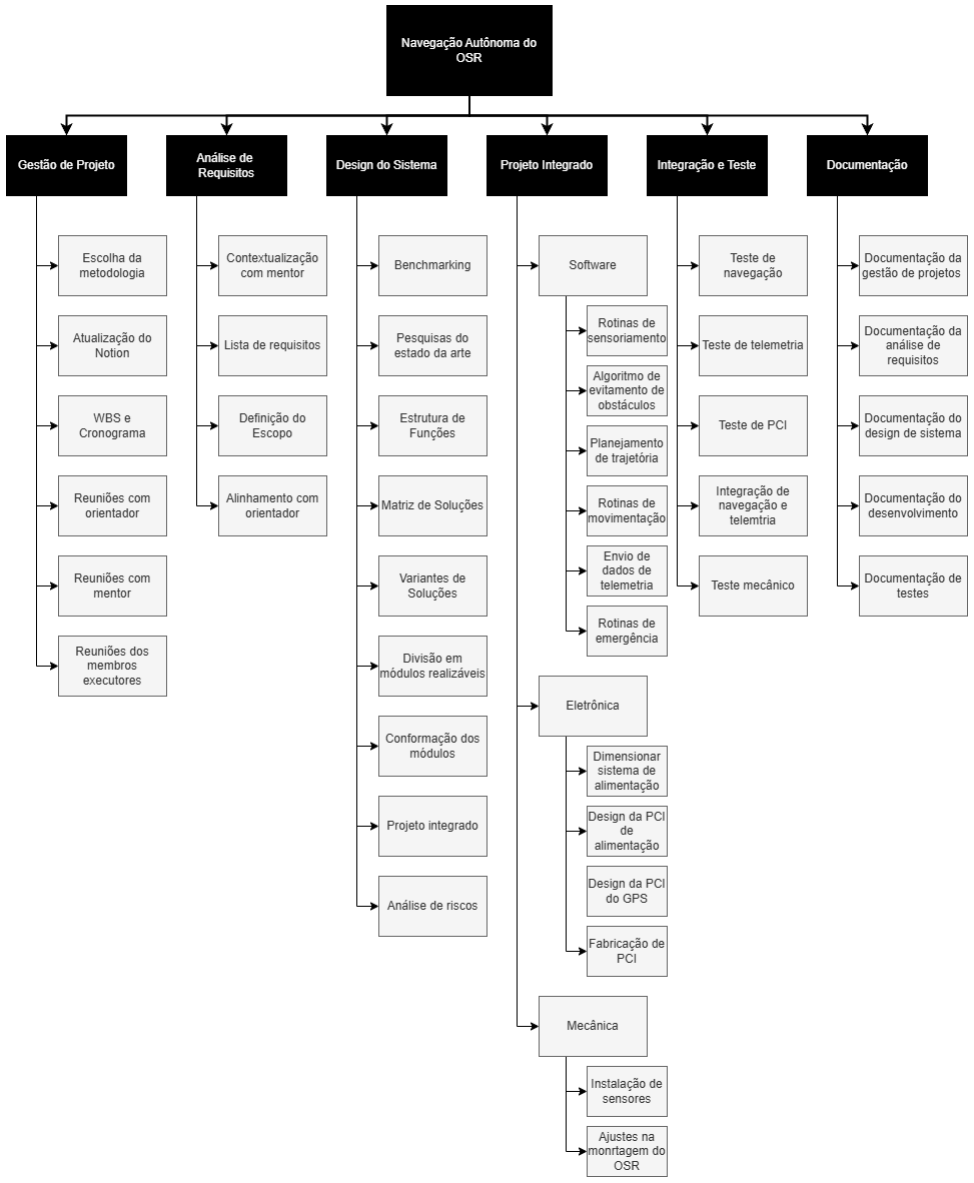
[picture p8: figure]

Figura 8 - Work Breakdown Structure (WBS) criado pela equipe (autoria própria)

Com todos as tarefas organizadas é possível estabelecer um tempo de realização para

cada uma delas baseado no que os integrantes do grupo acreditaram ser o necessário para cada

tarefa, assim podendo organizar quando cada parte do projeto deve ser iniciada e finalizada

para que tudo seja entregue. Foi estabelecido que dia 02/10, o dia da banca intermediária, será

o primeiro Gate do projeto, e dia 21/11 será o Gate final.

Figura 9 - definição dos gates de acordo com a metodologia Pahl & Beitz (autoria própria)

Com o WBS feito e os Milestones decididos, as tarefas foram divididas entre os

membros e foi definido um cronograma a ser seguido pela equipe.

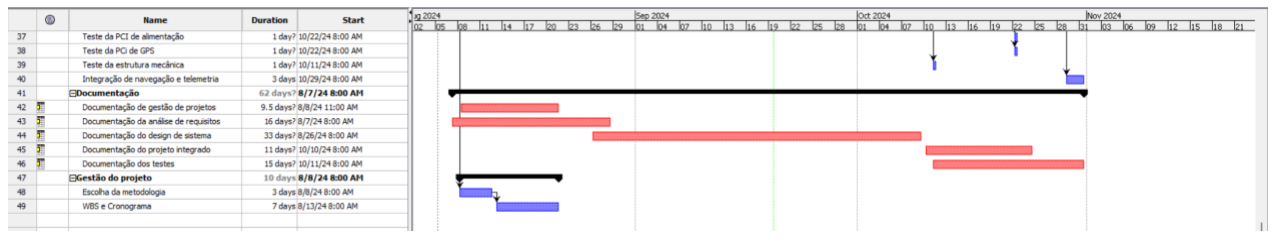
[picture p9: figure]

Figura 10 - cronograma criado pela equipe (autoria própria)

### 3 Desenvolvimento e gestão do Projeto

3.1 Lista de Requisitos e Elaboração das Funções

Seguindo a metodologia de Pahl & Beitz escolhida, inicialmente foi desenvolvida uma

lista de requisitos para o projeto, com o objetivo de elencar as necessidades técnicas e

exigências do cliente.

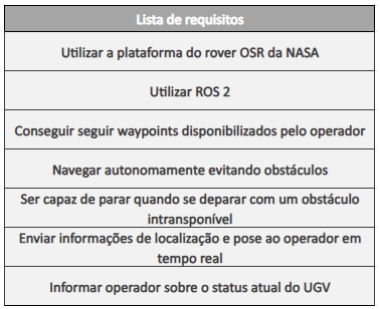
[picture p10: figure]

Figura 11 - Lista de requisitos (autoria própria)

Seguido da lista de requisitos é necessário determinar a função global do projeto para

então dividi-lo em subfunções que vão compor a totalidade do funcionamento do robô. A

função global é o objetivo principal que se tem com o projeto considerando as entradas e saídas

do sistema, mais especificamente de energia, sinais e materiais, no caso, a função global é a

navegação autônoma do robô, considerando que há entrada de energia elétrica de waypoints e

grandezas do ambiente e saída de movimento, ruído, luzes, dados de posição e pose do robô e

informações de status. Não há entrada e saída de materiais.

Figura 12 - Função global (autoria própria)

Após isso, a função macro do projeto que é a navegação autônoma foi dividida em

subfunções para esquematizar todos os processos que são necessários para que a navegação

autônoma ocorra. Assim, o esquema foi dividido em quatro partes, a que ocorre no robô e a que

ocorre em um ambiente de controle, a intermediação entre essas partes e a interface com o

usuário.

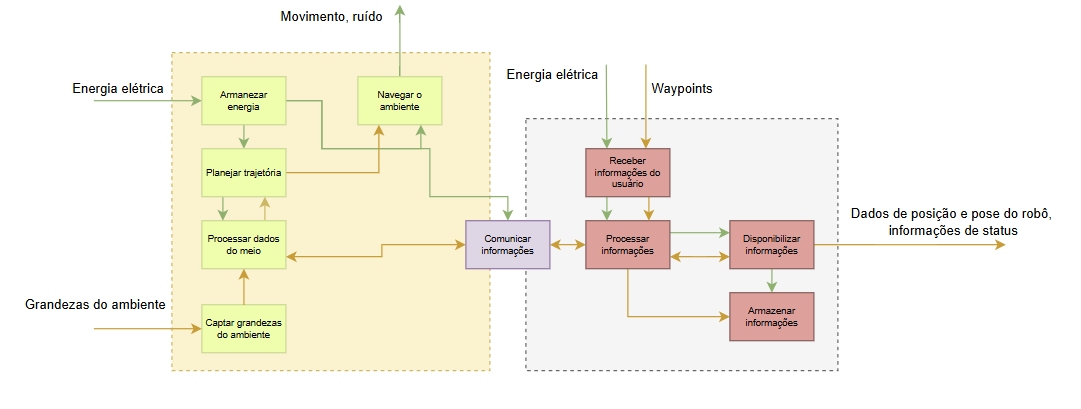
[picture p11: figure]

Figura 13 - Estrutura de funções (autoria própria)

Além disso, existe uma legenda para facilitar a compreensão do esquema da figura 12.

Figura 14 - Legenda da estrutura de funções (autoria própria)

3.2 Matriz de soluções

Com isso, é possível que se inicie a elaboração da matriz de soluções que inclui ideias

para resolver cada uma das subfunções apresentadas, obtidas através de pesquisas e

conhecimentos prévios. Assim, obtém-se variantes de solução para que então a melhor opção

seja selecionada de acordo com critérios previamente elaborados.

A matriz de soluções é dividida em três, o subsistema de processamento de dados e

planejamento de trajetórias, o subsistema de energia e movimentação e o subsistema de telemetria e IHM (Interface Homem-Máquina) para maior organização de informações. Cada

um desses subsistemas possui subfunções relacionadas a eles e cada uma das subfunções seus

blocos, ou seja, partes que compõe aquela subfunção. Assim, é possível indicar soluções para

cada um dos blocos, ao invés de uma solução mais geral para cada subfunção. Essa divisão foi

pensada com base no projeto do capstone de 2024.1 do peixe robô (Versolato et al., 2024, p.

48).

Figura 15 - Matriz de soluções do subsistema de processamento de dados e planejamento de trajetória (autoria própria)

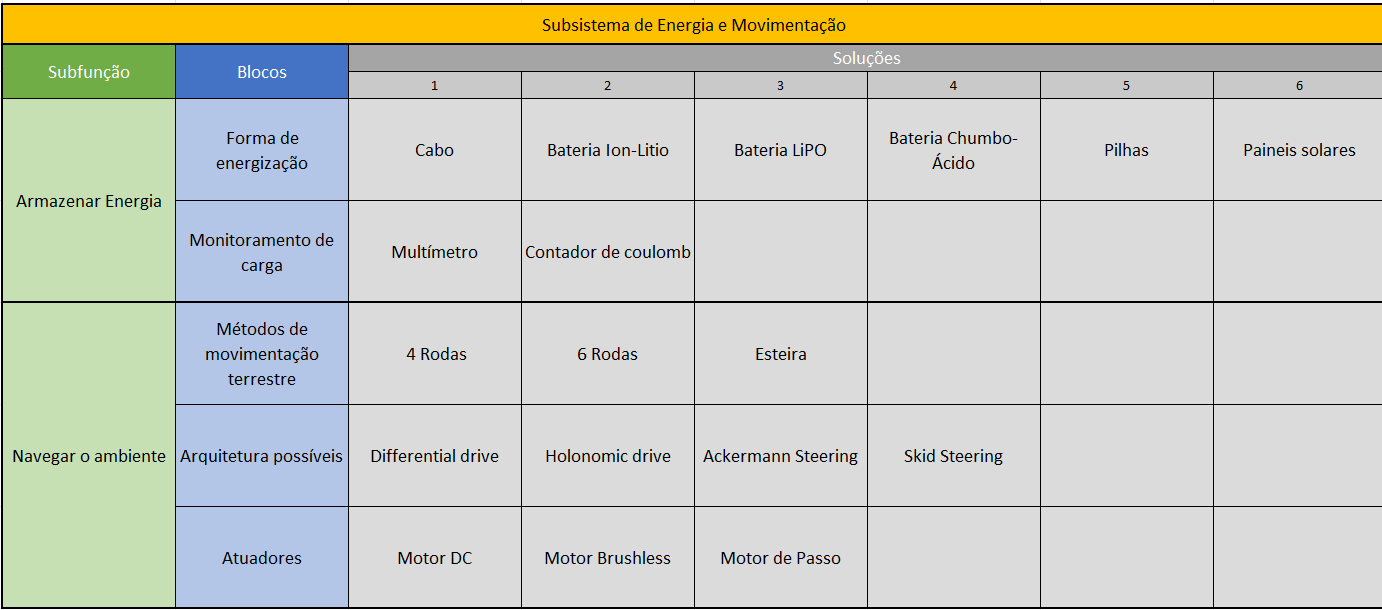
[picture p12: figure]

Figura 16 - Matriz de soluções do subsistema de energia e movimentação (autoria própria)

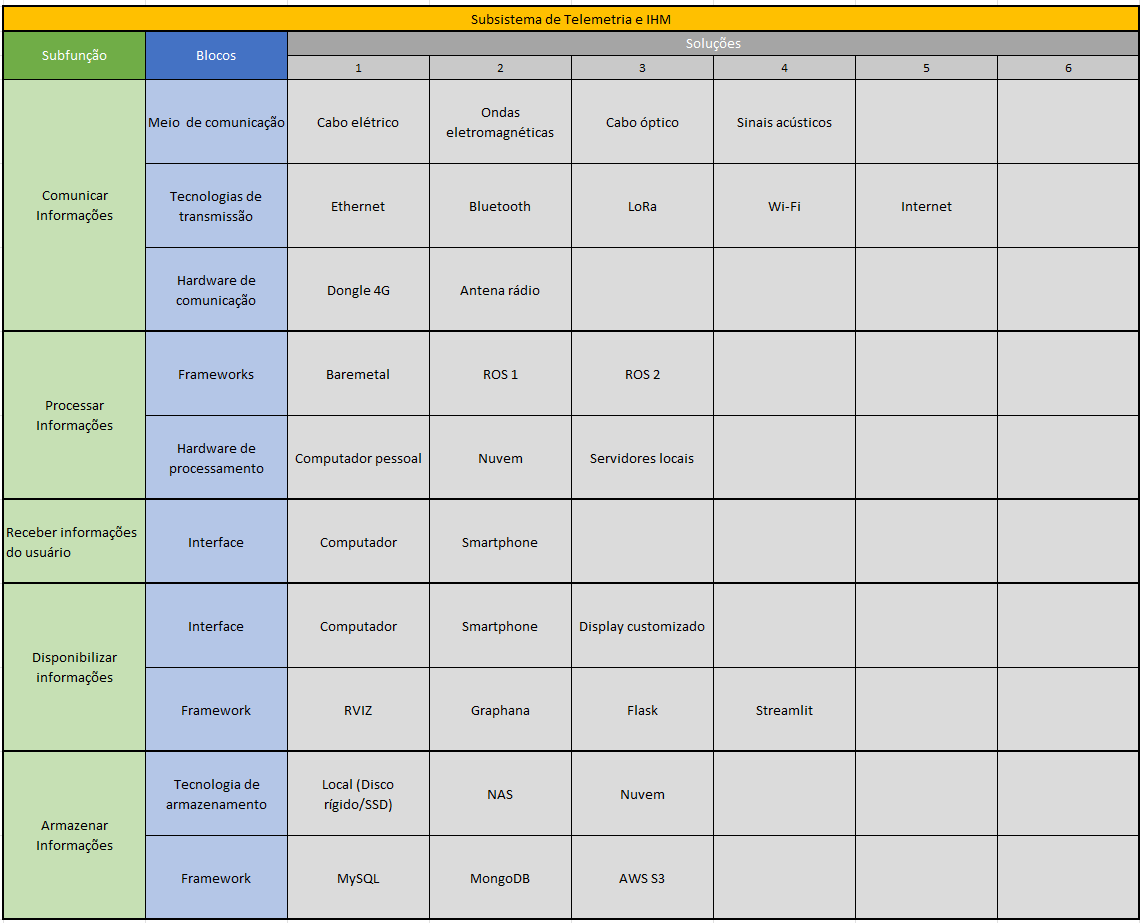
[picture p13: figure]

Figura 17 - Matriz de soluções do subsistema de telemetria e IHM (autoria própria)

3.3 Redução da Matriz de Soluções

Para selecionar a solução ideal segue-se a metodologia explicada a seguir. Com as

matrizes prontas, é realizada uma redução preliminar, onde são eliminadas soluções

inconsistentes e que não seguem os requisitos selecionados. Para essa redução é levado em

conta aspectos de segurança, ergonomia, produção, controle, montagem, transporte,

manutenção, reciclagem, gastos e entre outros aspectos importantes, gerando um critério de

avaliação das soluções. Após isso, são definidas métricas de avaliação mais específicas para

cada uma das soluções fazendo com que reste apenas as melhores. No final, isso são montadas

variantes de solução, que são as combinações possíveis entre as soluções restantes e cada uma

das variantes passa por uma avaliação de acordo com critérios definidos pelo grupo para que

então a melhor combinação de soluções seja escolhida.

A primeira redução feita foi excluindo as soluções que não vão de acordo com os

requisitos do projeto, dessa forma, o que está em amarelo nas imagens seguintes representa

aquilo que é necessário ser utilizado, assim, todas as outras possíveis soluções das respectivas

linhas podem ser eliminadas. Após isso, foi eliminado aquilo que se mostrava inviável para o

projeto, por conta de preço, tempo, manutenção, segurança, entre outros aspectos, o que está

representado em vermelho nas imagens.

Figura 18 - Redução da matriz de soluções do subsistema de processamento de dados e planejamento de trajetória (autoria própria)

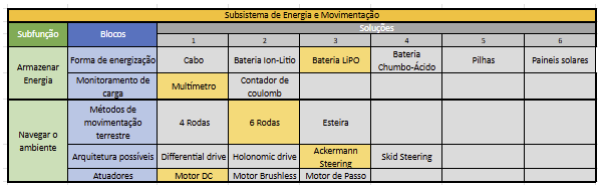
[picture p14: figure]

Figura 19 - Redução da matriz de soluções do subsistema de energia e movimentação (autoria própria)

Figura 20 - Redução da matriz de soluções do subsistema de telemetria e IHM (autoria própria)

Após essa redução preliminar, continuou-se o processo. Para isso, foi utilizado métricas

para definir quais opções não eram bons o suficiente em comparação com as demais. Uma vez

definida as métricas, o grupo analisou cada solução que passou pela redução preliminar e

definiu uma nota para cada métrica definida. As soluções em que todas as métricas tiveram uma

nota positiva foram selecionadas para definir as soluções. Na Figura 21 está o resultado deste processo e no Apêndice A – REDUÇÃO DA MATRIZ DE SOLUÇÕES está a redução

completa da matriz de soluções.

Figura 21 - Resultados da redução da matriz de soluções (autoria própria)

Com as soluções reduzidas, é possível formar as variantes de solução, que estão

ilustradas nas figuras a seguir:

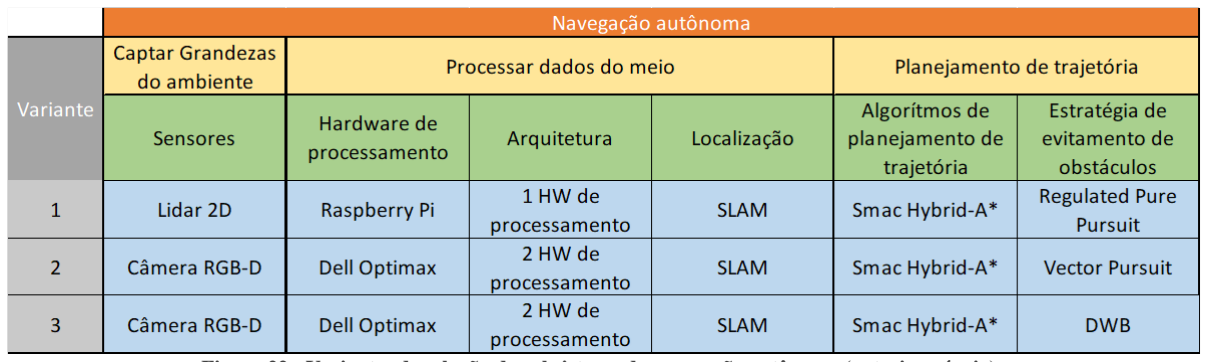
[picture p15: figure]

Figura 22 - Variantes de solução do subsistema de navegação autônoma (autoria própria)

Figura 23 - Variantes de solução do subsistema de telemetria e IHM

A primeira variante representa algo que o grupo considera mais simples, a terceira

representa a variante ideal e a segunda um intermediário entre os dois. Assim, através de uma

análise, a variante selecionada foi a segunda.

3.4 Escolha de sistema operacional e distribuição de ROS para o módulo de navegação

A versão do ROS utilizada é a ROS 2 Humble Hawksbill, que oferece suporte para os

seguintes sistemas operacionais: Windows 10, Ubuntu 22.04 Jammy e Red Hat Enterprise 8. A

versão do módulo de navegação foi mantida em relação a iteração anterior para permitir a

comunicação com a Raspberry Pi do módulo, dado que não existe suporte oficial para a

transmissão de dados entre distribuições diferentes do ROS (ROS CROSS-DISTRIBUTION

COMMUNICATION, 2022).

A escolha se deu principalmente pela disponibilidade de binários prontos para os

pacotes ROS, uma vez que existe garantia que o ambiente de desenvolvimento será replicável

entre diferentes computadores usando o mesmo sistema operacional. Segundo o padrão REP

143 (REP 143, 2014), todos os pacotes ROS oficiais devem estar disponíveis dentro da

plataforma Rosdistro. Até o momento, o Windows nunca recebeu suporte na plataforma

Rosdistro. Até 2021, com o lançamento da distribuição ROS 2 Galactic Geochelone, a

plataforma apenas oferecia suporte para sistemas operacionais Ubuntu, sendo que até o

momento atual nem todos os pacotes oficiais foram portados para Red Hat. Portanto, entre os

três, foi escolhido o Ubuntu 22.04.

3.5 Configuração de sensores

Antes de serem usados, os sensores precisam estar configurados e calibrados

corretamente. Segue as instruções para o preparo de cada sensor.

Figura 24 - Intel Realsense D435i (fonte: ntelrealsense, 2019)

Para a configuração da Realsense D435i é necessário calibrar o seu IMU, que não vem

com calibração de fábrica (GETTING IMU DATA FROM D435I AND T265, 2021). Um script

Python de calibração está disponível no repositório do kit de desenvolvimento de software da

Realsense, chamado Librealsense. O arquivo rs-imu-calibration.py está contido no diretório

tools e depende da biblioteca pyrealsense2.

O script espera que o usuário posicione a câmera em 6 orientações diferentes, mantendo

o dispositivo parado até atingir a estabilização necessária. As orientações necessárias estão

descritas em um guia da Intel (INTEL REALSENSE DEPTH D435I IMU CALIBRATION,

2019). Por fim é atribuída uma nota a qualidade da calibração, sendo considerada uma nota boa

valores próximos de 98. A nota atingida foi de 98.05.

Além disso, vale ressaltar que a Realsense D435i é composta por duas câmeras

infravermelho, uma câmera RGB e um emissor infravermelho, que podem ser configurados

usando um arquivo YAML (INTEL REALSENSE D435i, 2024). Existem dois modos

principais de uso como câmera de profundidade.

O primeiro, RGB-D baseado em de luz estruturada, usa a câmera RGB para fornecer

dados visuais e o conjunto de emissor e câmeras infravermelho para emitir uma textura

infravermelho e estimar a profundidade pela análise de como a textura está sendo projetada no

ambiente (ROBOTICS TOMORROW, 2018). O segundo, que apenas utiliza as câmeras

infravermelho, é baseado na técnica de triangulação, sendo capaz de estimar a profundidade ao

identificar a posição dos mesmos pontos de interesse nas imagens das duas câmeras e combinar com dados internos da calibração da Realsense como foco e distância entre as câmeras

(FIDLER, 2015).

O arquivo YAML pode ser usado para configurar parâmetros internos como tempo de

exposição, resolução da imagem, entre outros. Para o modo de uso da câmera infravermelho a

conflagração foi essencial, dado que o emissor de texturas é ligado por padrão e interfere com

os dados da imagem, precisando ser desligado.

Ao realizar testes, percebeu-se que as câmeras infravermelho possuem um maior campo

de visão. Além disso, a câmera RGB tende a ter artefatos de granulação em ambientes com

menor iluminação.

Figura 25 - LiDAR LDS-02 (fonte: ROBOTIS e-Manual, 2024)

Em relação ao LiDAR LDS-02, é necessário configurar as regras de udev para permitir

seu funcionamento. As regras de udev servem para executar scripts em resposta a eventos de

dispositivos, como conectar ou desconectar um cabo de uma entrada USB (AN

INTRODUCTION TO UDEV: THE LINUX SUBSYSTEM FOR MANAGING DEVICE

EVENTS, 2018). O arquivo de configuração 99-turtlebot3-cdc.rules se encontra no repositório

Robotis/turtlebot3, dentro do pacote turtlebot3_bringup.

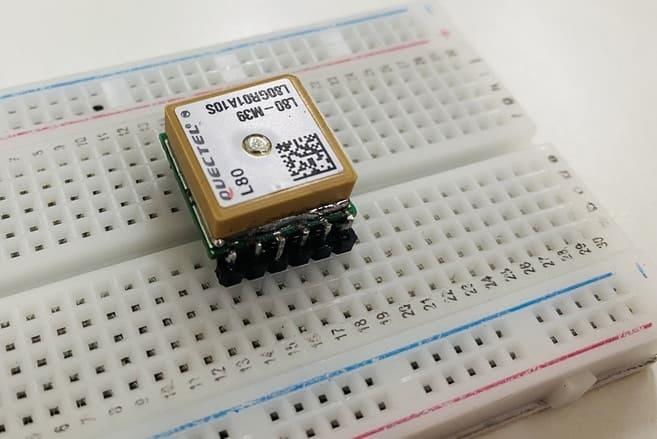
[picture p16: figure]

Figura 26 - GPS Quectel L80 M39 (fonte: how2electronics, 2023)

Para que seja possível ter um monitoramento da posição do UGV durante sua operação,

a equipe adquiriu um dispositivo GPS chamado GPS3 Click que conta com um módulo Quectel

L-80 M39. Este módulo tem precisão de posicionamento menor que 2,5 metros e tem baixo

consumo de energia. Após testes com o dispositivo, se viu que sem uma antena externa, o

módulo tem dificuldade de se conectar a satélites, sendo quase inutilizável em ambientes

fechados.

3.6 Criação do pacote osr_autonomous

Com o ambiente ROS e os sensores preparados, o próximo passo necessário é rodar os

nodes ou nós, os arquivos executáveis de um pacote ROS, com os parâmetros desejados para

inicializar a solução do projeto. Um nó pode ser executado a partir do terminal com o comando

ros2 run nome_do_pacote nome_do_executável. Entretanto, para um caso de uso complexo

como o do projeto atual, que exige um uso de diversos nós e uma variedade de parâmetros

customizáveis, é uma boa prática criar um pacote próprio e estruturar a aplicação com arquivos

launch.

Arquivos de launch realizam a orquestração de uma aplicação, executando todos os nós

e seus respectivos parâmetros com um só comando. No ROS 2, o formato dos arquivos de

launch mudou de XML para Python, possibilitando implementações de lógica que a linguagem

de markup não permitia. Com isso em mente, foi criado um pacote chamado osr_autonomous

para manter os arquivos de launch e eventuais arquivos YAML para a configuração de certos

pacotes, como o NAV 2.

Foram elaboradas versões de launch diferentes entre si para testar as diferentes

combinações de sensores. Nisso se inclui versões com as combinações possíveis de câmera

RGB, câmera infravermelho e fusão de sensores Visual-Inercial.

A seguir irá ser mencionado o papel de cada pacote ROS integrado nos arquivos launch

e para isso irá ser descrito o launch com fusão de sensores, dado que todos os pacotes do outro

launch estão contidos nele.

Os primeiros nós a serem incluídos no launch foram os relativos aos sensores. O pacote

realsense2_camera foi utilizado com parâmetros para a publicação de imagens RGB, dados de

profundidade, giroscópio e acelerômetro. Também foi configurada a opção que permite a sincronia dos dados de giroscópio e acelerômetro, que são publicados a uma taxa diferente, 200

Hz e 62.5 Hz respectivamente. Em seguida, o pacote imu_filter_madgwick recebe os dados da

Realsense e une as informações de velocidade angular e aceleração para estimar a orientação

da câmera com base em quaterniões.

Em seguida, é necessário configurar as transformações do sistema de coordenadas dos

sensores para o base_link, o ponto de referência do UGV que fica em seu centro. Para isso é

utilizado o pacote tf 2, que é nativo do ROS e é capaz de publicar transformações estáticas entre

dois sistemas de coordenadas. Desse modo, informações como a odometria visual da câmera

podem ser projetadas para o ponto de referência do veículo.

Também foi utilizado o pacote robot_state_publisher para publicar as transformações

entre as juntas do robô e o base_link. Esse tipo de transformação não é estático, uma vez que a

orientação das juntas pode mudar dependendo do estado do robô. Os dados de posicionamento

das juntas já são publicados pela Raspberry Pi desde a iteração anterior do projeto.

Figura 27 – árvore de transformações

Além disso, foi utilizado a framework NAV 2 para as tarefas de planejamento de rotas.

Foram utilizados os plugins de planejamento global, planejamento local, árvore de

comportamentos, suavização de rotas e monitoramento de colisões.

Vale ressaltar que o NAV 2 utiliza um sistema de configuração de parâmetros baseado

em arquivos YAML. O framework espera parâmetros envolvendo planejadores de rota,

controladores de trajetória local, mecanismos de recuperação, entre outros.

Outro pacote utilizado foi o navsat_transform, que publica a transformação geométrica

entre o sistema de coordenadas local e o Sistema Universal Transversa de Mercator (UTM),

que será detalhado adiante.

Também foi desenvolvido pela equipe um nó customizado que usa a biblioteca ROS

Geodesy para receber waypoints em coordenadas de GPS no formato WGS84 e traduzi-los para

o sistema de coordenadas local. Isso será detalhado mais adiante.

Por fim, o RTAB-MAP é utilizado para realizar os processos de SLAM e odometria

visual. Os testes de parâmetros serão detalhados a seguir.

3.7 Testes de parâmetros com RTAB-MAP

Para a realização de testes iniciais com os parâmetros foi utilizado um computador com

uma AMD Ryzen 7 4800H, que tem oito núcleos e clock base de 2.9 GHz, e 16 GB de RAM

DDR4 de frequência 3200 MT/s. O intuito desses testes é encontrar os melhores parâmetros

para uma condição com um poder computacional considerável, para ter uma base de

comparação na escolha do computador a ser instalado no veículo.

O primeiro teste foi feito com as condições padrão do RTAB-MAP para SLAM e

odometria visual. Essas condições são: mapeamento em 6 graus de liberdade (3D), coleta de

features visuais com keypoints no formato GFTT e descriptors no formato ORB para uso em

etapas de odometria e geração de mapas locais, taxa de atualização do mapa global de 1Hz e

odometria visual no modo Frame to Map (F2M), que compara os dados do frame atual com features de múltiplos frames anteriores para estimar a odometria (LABBÉ, 2019).

Para estimar a qualidade dos testes foi utilizado o comando ros2 topic hz /odom para

monitorar a taxa de publicação da odometria visual e foi utilizado o RViz para verificar se

mapeamento está condizente com a realidade.

Sob essas condições, o computador conseguiu processar o nó de odometria visual com

uma média de 10 Hz. Em relação ao desempenho, observou-se que o sistema perdia a referência

de odometria visual ocasionalmente, principalmente quando se aproxima de ambientes com

pouca variedade de cor ou em casos de movimento rápido da câmera. O primeiro caso se deve a extração de features, o qual é prejudicado em ambientes com pouca diferenciação. O segundo

caso pode ter sido causado por baixas taxas de publicação de odometria ou de atualização do

mapa. Entretanto, o funcionamento pode ser considerado relativamente satisfatório com o uso

do modo F2M, que é capaz de realizar a recuperação da odometria.

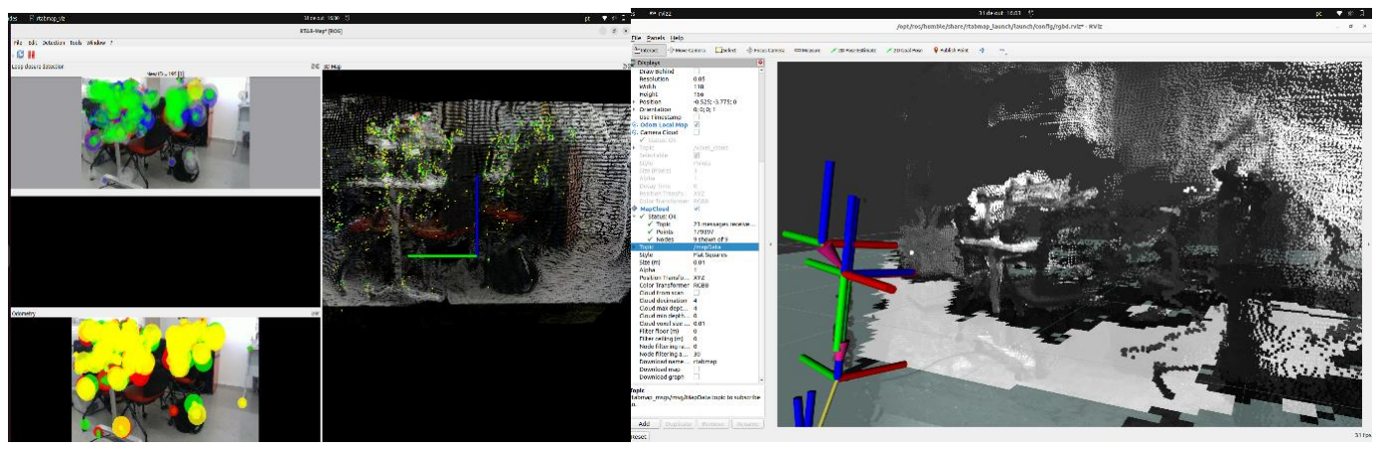
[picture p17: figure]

Figura 28 - Resultados de SLAM com RTAB. A esquerda é está o visualizador rtabmap_viz, com uma representação das features e da odometria. A direita o RViz está configurado para mostrar o mapa em Point Cloud e a projeção para Occupancy Grid

Foram também testadas opções menos complexas para o cálculo da odometria visual,

com o fim de aumentar a taxa de publicação. A escolha dos parâmetros a serem testados foram

baseadas em guias oficiais da plataforma no site ROS Org (Mathieu Labbe, 2023) e na página

do GitHub do RTAB-MAP.

Os testes utilizaram o modo Frame To Frame (F2F), que compara o frame atual apenas

com o anterior. Outros parâmetros configurados foram o número máximo de features e o uso

de técnicas de optical flow para analisar o movimento do frame como todo sem a necessidade

de usar descriptors e comparar as features em si. Essas mudanças em específico conseguiram

simplificar o processo de calcular a odometria visual, gerando uma taxa média de 28 Hz.

Entretanto, a odometria visual é perdida com maior facilidade devido ao sistema F2F e a coleta

de features simplificada.

Uma solução robusta deveria ser um caso intermediário, capaz de oferecer uma taxa

adequada de odometria, ser capaz de retomar sua referência quando perdida e conseguir coletar

um conjunto de features suficiente para calcular a transformação entre dois frames e estimar a

pose atual.

Para isso foram escolhidos os seguintes parâmetros: mapeamento em 3 graus de

liberdade (2D), projeção de mapas locais para 2D, taxa de atualização do mapa em 10 Hz,

features que usam o método ORB de keypoints e descriptors, coleta de no máximo 1000 features por quadro e uso da técnica F2M para comparação do quadro atual com múltiplos

quadros anteriores. Esses parâmetros geraram um resultado satisfatório e com uma taxa de

publicação de odometria média de 16 Hz e um valores mínimos e máximos observados de 14 e

25 Hz, respectivamente.

Após esse processo foi realizado uma comparação entre os arquivos launch. Em relação

ao uso da unidade inercial, a principal diferença observada é que a versão com IMU aparenta

perder a referência da odometria visual com menos frequência ao realizar movimentos bruscos.

Já em relação aos modos da Realsense, foi observado que o modo de câmera

infravermelho com a técnica de triangulação gera ruídos no mapa com menos frequência do

que o modo de luz estruturada com RGB-D. Isso pode ser consequência do campo de visão das

câmeras infravermelho ser maior que o da câmera RGB-D e ter menor tendência a gerar

artefatos de granulação. Seria necessário formalizar uma métrica para afirmar isso

categoricamente.

É reconhecido pelos autores deste texto que não foram utilizadas métricas formais para

os resultados apresentados dos testes realizados. Isso é um ponto que pode ser melhorado e

explorado em futuras iterações do projeto.

3.8 Seleção de computadores para o módulo de navegação autônoma

Um dos objetivos de usar um módulo separado para navegação é garantir que os

recursos computacionais sejam suficientes para executar as tarefas. A placa responsável pelos

processos de alto nível do UGV no módulo base é a Raspberry Pi 4B. Esse modelo possui dois

núcleos, roda a 1.5 GHz em frequência de clock base e possui 8 GB de memória RAM (Rasberry

Pi 4 Model B, 2024), o que pode ser considerado limitado para tarefas de navegação.

Pode se observar uma tendência de uso de computadores com maior poder

computacional nesse meio. Considerando aplicações de mercado, como os UGV’s Husky e

Warthog da Clearpath Robotics (CLEARPATH ROBOTICS, 2024) ou o RB-VOGUI da

Robotnik (ROBOTNIK, 2024), que usam processadores dedicados da Intel ou placas Nvidia

Jetson. Além disso, a atuação dos motores do veículo é uma tarefa crítica que não deve ser

comprometida pelo processamento de tarefas de alto nível, então a separação em módulos traz

uma segurança nesse sentido.

Foi realizado uma pesquisa de computadores disponíveis no Insper para compor o

módulo de navegação autônoma. Inicialmente foram encontradas as seguintes opções: Nvidia

Jetson TX2 e Intel NUC D34010WYK. Para avaliar a usabilidade de cada uma foram realizados

testes para verificar sua performance.

3.8.1 Nvidia Jetson TX2
A linha Nvidia Jetson é uma série de placas de computação embarcada equipadas com

GPU’s dedicadas. As placas usam CPU’s de arquitetura ARM com foco em desempenho

energético. Essa linha é voltada para a área de robótica e computação de borda, possibilitando

aplicações de aprendizado de máquina e computação visual em dispositivos embarcados

(NVIDIA, 2024).

O Kit de desenvolvimento Jetson TX2 é uma placa que já passou do período de fim de

vida, que acabou em 2020 (NVIDIA DEVELOPER, 2020). A versão disponível mais recente

do Linux for Tegra (L4T), o sistema operacional proprietário baseado em Ubuntu com drivers

Nvidia embutidos, não é baseado em Ubuntu 22.04, sendo limitado ao funcionamento do

Ubuntu 18.04. Apesar dessa versão de sistema operacional não ter suporte para o ROS 2, foi

encontrado um repositório mantido por um funcionário da Nvidia com descrição de contêiners

Docker especializados para o uso de ROS na linha Jetson (FRANKLIN, 2024).

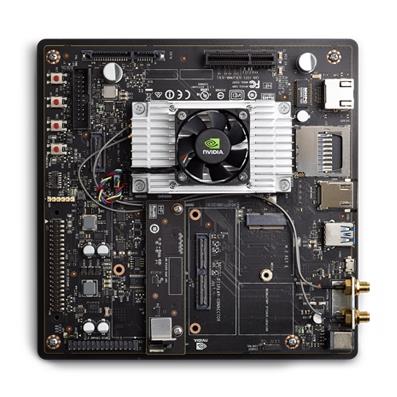
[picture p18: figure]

Figura 29 - Jetson TX2 developer kit (fonte: siliconhighwaydirect)

Dentre eles, existe um contêiner de ROS 2 Humble para o L4T 32.7.1 que pode ser

utilizado. A maior problemática desse uso seria que a plataforma Rosdistro não oferece binários

de pacote ROS para sistemas L4T, portanto todas as dependências devem ser compiladas do código fonte. Entretanto, o uso de conteinerização do Docker ofereceria a replicabilidade

desejada e facilidade de deploy.

A placa foi recebida com L4T 28, uma versão baseada em Ubuntu 16.04. Para o uso do

contêiner foi necessário a instalação da versão mais recente do L4T com o uso da aplicação

Nvidia SDK Manager. A aplicação apresentou erros na instalação da imagem do sistema

operacional, não configurando interfaces de rede e serviços necessários para a continuação do

instalador, como o SSH. Esse tipo de erro é reconhecido pela Nvidia na instalação da versão

desejada e a empresa não ofereceu uma solução definitiva para isso, apenas soluções de

contorno que podem gerar instabilidades (NVIDIA DEVELOPER, 2019).

Manualmente criando o serviço SSH e usando a interface de rede local sem fio (WLAN)

para estabelecer a comunicação com computador executando o Nvidia SDK Manager foi

possível prosseguir com a instalação. Entretanto, foram encontradas ainda mais instabilidades

de rede que impossibilitavam o estabelecimento de conexão Ethernet, algo crucial para a

comunicação com o módulo base. Novamente, a Nvidia reconhece o erro e oferece apenas uma

solução de contorno, que consiste no uso de IP’s estáticos em uma configuração de rede

específica (NVIDIA DEVELOPER, 2019). Tendo em vista as instabilidades das versões mais

recentes do ambiente Jetson para o modelo TX2, somado ao fato do ambiente já não ter suporte

oficial ao ROS 2, foram procuradas outras opções de computadores.

3.8.2 Intel NUC D34010WYK
A linha Intel NUC é especializada em minicomputadores, pensados para uso em

escritórios ou para computação de borda, dependendo do modelo. Os computadores possuem

processadores com arquitetura x86 e possuem desde versões com menor desempenho, como as

da linha Intel Celeron, até versões de alto desempenho da linha Intel Core I9. A Intel

desenvolveu os produtos NUC até 2023, no ano em que a empresa ofereceu os direitos de

licenciamento para a ASUS.

A Intel NUC disponível é de um modelo produzido em 2013, o ano em que a linha NUC

foi lançada. O modelo não recebe mais suporte da Intel ou ASUS, atingindo o seu fim de vida

em 2018. Essa NUC tem um processador Intel Core i3-4010U que possui dois núcleos e clock

básico de 1.7 GHz.

Figura 30 - Intel NUC 2013

Foram realizados dois testes com parâmetros diferentes do RTAB-MAP, ambos com

desempenho consideravelmente baixo. O primeiro, com as condições padrões, obteve uma taxa

de publicação de odometria média de 0.8 Hz. O segundo, que usa as condições mais simples do

modo F2F e optical flow para o cálculo da odometria, atingiu uma taxa de publicação média de

11 Hz.

O desempenho dos dois testes foi consideravelmente pior em relação a publicação da

odometria, que estava a 10 Hz e 28 Hz no notebook, respectivamente. Em relação à qualidade

do mapeamento, notou-se que a referência da odometria era perdida com uma frequência

consideravelmente maior que no notebook, principalmente no segundo teste. Isso é grave dado

que os processos de mapeamento e navegação autônoma dependem diretamente da

disponibilidade da odometria.

Não foi realizado um teste com os parâmetros finais escolhidos, uma vez que eles foram

decididos em um tempo posterior. Entretanto, a partir dos dados coletados nos dois testes é

possível perceber que o poder computacional da Intel NUC é limitante para processar as tarefas

de SLAM e odometria visual.

3.8.3 Dell OptiPlex 7000 MFF
A série OptiPlex de computadores Dell é voltada para uso empresarial, apresentando

uma variedade de modelos de chassi e processadores. O tamanho dos computadores varia entre

o tamanho de gabinete desktop com o modelo de chassi All-in-One, até o tamanho de um

minicomputador com os modelos Micro Form Factor e Ultra Form Factor.

Após os testes com a Intel NUC, alternativas de computadores foram procuradas em

laboratórios Insper. Foi encontrado o modelo OptiPlex 7000 MFF, que possui um processador

Intel Core i5-12500 de 6 núcleos e frequência de clock base 3 GHz. Em relação a memória, o

computador tem 8 GB de RAM DDR4 de 3200 MT/s.

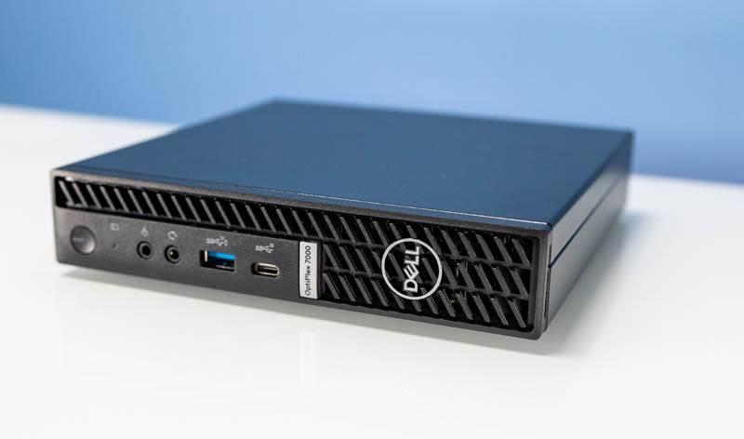
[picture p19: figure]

Figura 31 - Dell OptiPlex 7000 MFF (fonte: acdtech.mu)

A configuração desse minicomputador é mais próxima ao dos testes no notebook. O

desempenho de um núcleo individual desse modelo é superior ao do notebook testado.

Entretanto, a OptiPlex possui dois núcleos a menos no processador e metade da memória

disponível.

Ao executar o arquivo launch na Optiplex foi obtido um resultado semelhante ao do

notebook, com uma média de publicação de odometria entre 28 e 30 Hz. Tendo isso em mente,

a Dell Optiplex foi escolhida para ser o computador do módulo de navegação autônoma.

3.9 Ajustes elétricos para uso da Optiplex

Para que seja possível a utilização da Optiplex 7000MFF foi necessário adicionar um

circuito de alimentação responsável por ajustar a tensão da bateria de 14.8V para os 19.5V de

entrada do computador.

Diante deste problema, foi decidido utilizar uma configuração em que a tensão de

entrada seria amplificada através de um módulo regulador de tensão Step-Up, um dispositivo

de alta eficiência por sua natureza chaveada. Para achar o módulo adequado foi levado em

consideração a fonte original da Optiplex que tem como parâmetros a capacidade de fornecer

19.5V a 4.65A, ou seja, uma potência de 90W.

Figura 32 - Esquemático da alimentação da Optiplex
Após pesquisar diversas opções, se foi optado por utilizar um Step-Up, que tem

especificação de 10-32V de entrada e consegue fornecer 12-35V de saída, com a tensão de saída

sempre superior a entrada. O módulo também conta com uma amperagem máxima de entrada

de 10A e 6A de saída.

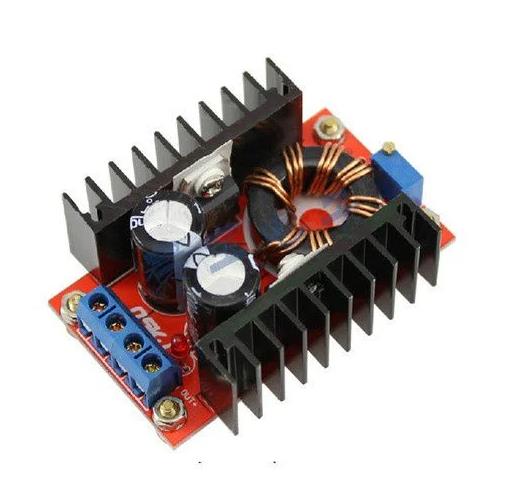
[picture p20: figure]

Figura 33- Módulo Step-Up utilizado

Por mais que este componente é teoricamente capaz de entregar o desempenho que era

necessário, por questões de robustez foi realizado um teste de bancada simulando a situação

limite, onde o módulo teria que prover os 19.5V e 4.65A por um período de tempo considerável.

Para isso foi montado um circuito utilizando uma fonte de bancada para fazer o papel da bateria

e um banco de resistores de potência para agir como a carga.

Figura 34 - Esquemático do circuito de teste do Step-Up (autoria própria, 2024)

Após os testes foi observado que dada essa situação limite, o módulo Step-Up atingiu

uma temperatura máxima superior a 70º C, o que foi julgado como inadequado. Portanto, foram

apresentadas duas soluções, alterar os componentes do módulo por especificações mais

extremas, ou adicionar resfriamento forçado. Imagens do teste capturadas por uma câmera

térmica estão disponíveis no apêndice B.

Considerando que os componentes necessários para fazer a troca eram difíceis de se achar e

não possuíam garantia de qualidade nem de tempo de entrega, foi optado por adicionar uma

ventoinha de 80mm para resfriar o interior do robô.

Figura 35 - UGV com sistema de resfriamento instalado

3.10 Ajustes mecânicos

Na parte superior do robô é necessário posicionar a OptiPlex, a câmera realsense e o

Lidar. Porém, a OptiPlex ja ocupa todo o espaço disponível, dessa forma foi projetada uma

caixa de acrílico com o intuito de proporcionar ao UGV um "segundo andar". Dessa forma, na

parte de cima são fixados os suportes dos sensores e na parte de baixo a OptiPlex.

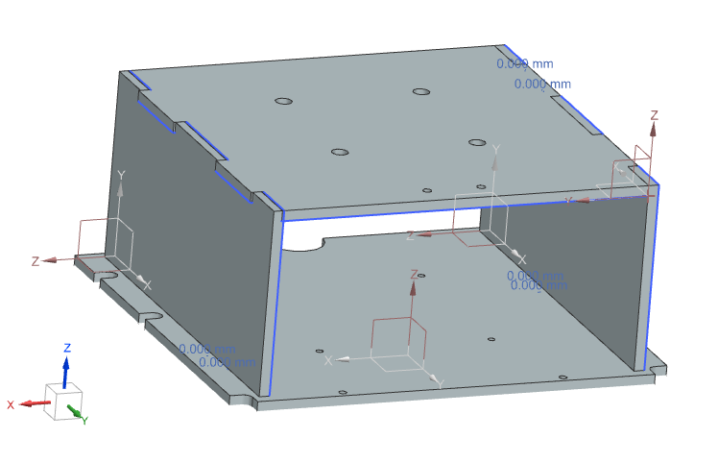
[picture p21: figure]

Figura 36 – Modelo 3D da caixa

Figura 37 - Caixa para fixação dos sensores e da Optiplex

Como a estrutura não permanecia completamente reta, ou seja, caso alguma força fosse

aplicada nas laterais a estrutura iria se mover, o que não é ideal para a aplicação em questão, e

não era possível colar tudo por conta da dificuldade de montar e desmontar caso tudo estivesse

colado, foi posicionado 4 estruturas metálicas em "L" que forçavam a caixa a permanecer em

90 graus tornando a estrutura mais estável.

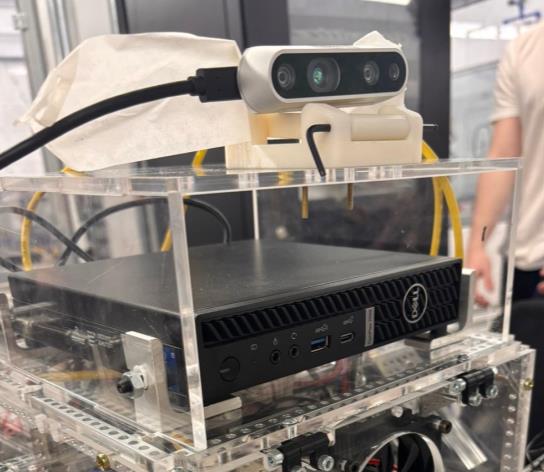
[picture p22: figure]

Figura 38 - Caixa montada no robô com estruturas em "L" para estabilidade

Além disso, com as estruturas em "L" a OptiPlex ficou 12 mm mais alta nas laterais, já

que elas possuem 6 mm assim como a cabeça do parafuso, dessa forma foram adicionadas duas

placas quadradas de acrílico de espessura de 6 mm para deixar tudo no mesmo nível.

Por fim, a estrutura já existente foi modificada para receber a ventoinha e rasgos nas

laterais para exaustão.

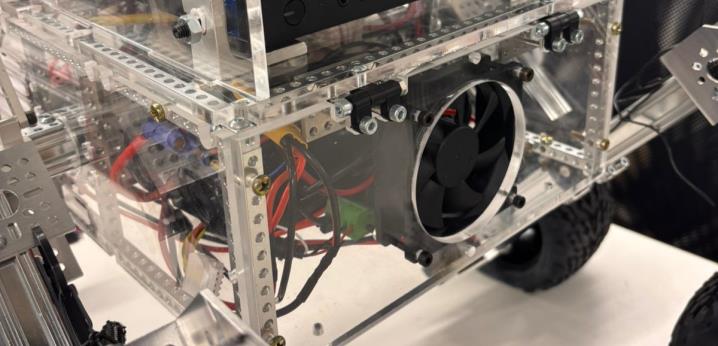
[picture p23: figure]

Figura 39 - Espaço na estrutura para a ventoinha

Figura 40 - Modelo 3D das laterais com rasgos para exaustão

Todos as partes foram projetadas no software NX Siemens e após transformar o arquivo

em DXF foram cortadas na cortadora a laser.

3.11 Interface Humano-Robô e RViz

Como interface humano-robô foi utilizada a aplicação RViz. A ferramenta é o

visualizador padrão para o ROS, capaz de se inscrever em tópicos para o recebimento de dados

e de representá-los visualmente em 3D. O RViz possui padrões de visualização para os formatos

de mensagem ROS mais comuns como odometria, pose e point cloud, entre outros. Além disso,

é possível configurar plugins customizados para representar um formato de dados visualmente,

o que é utilizado pelo RTAB-MAP, por exemplo, para incorporar associação de point cloud

com imagem RGB.

Outro papel interessante do RViz é sua associação com o pacote NAV 2. O RViz

permite publicar dados de Pose 2D como objetivos de navegação e enviá-los ao canal esperado

pelo NAV 2. Entretanto, isso não é suficiente para publicar uma trajetória de waypoints, dado

que apenas um ponto serve como objetivo. Para resolver essa questão, um plugin de RViz

oficial do pacote NAV 2, waypoint_follower, foi desenvolvido.

O NAV 2 possui um arquivo de launch pronto em seu pacote de bringup para inicializar

seus plugins. Nele é possível visualizar informações como trajetórias locais e globais, footprint

do robô e odometria. O plugin waypoint_follower também está disponível para publicar os

waypoints.

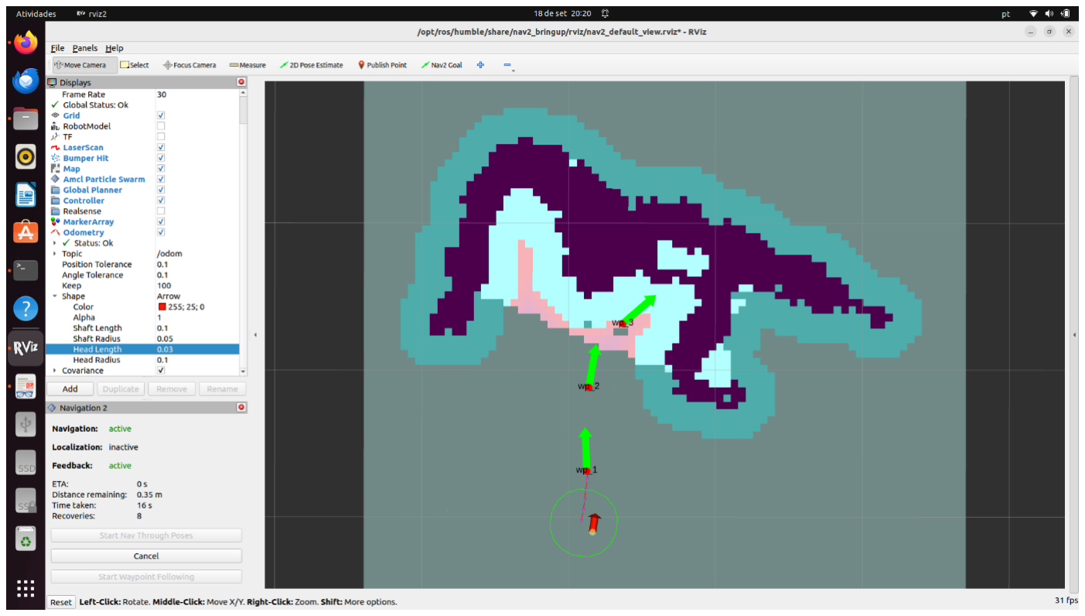
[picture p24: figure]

Figura 41 - Ambiente RViz configurado com plugins NAV 2. A circunferência representa a footprint do robô, a seta vermelha representa a odometria, a seta roxa representa a trajetória computada e os pontos vermelhos são os Waypoints

Também foi testado a comunicação entre computadores. Para isso, dois computadores

se conectaram na mesma rede local: um rodando o launch do projeto e outro rodando apenas o

RViz. O ROS 2 permite que qualquer dispositivo encontre outros dispositivos na mesma rede

de forma descentralizada, sem a existência de um processo externo que organize isso. Para

comparação, o ROS 1 usava o comando roscore para configurar o ROS Master, o processo

principal de descoberta de tópicos, e qualquer máquina que desejasse se comunicar deveria

informar o endereço do master. Portanto, apenas conectar os dispositivos na mesma rede é o

suficiente para permitir a transferência de dados entre os computadores.

Em relação ao NAV 2, inicialmente, a documentação oficial do NAV 2 (NAV2, 2023)

foi consultada para a configuração de parâmetros, sendo que apenas os planejadores locais e

globais foram configurados considerando características específicas do projeto, como o

objetivo de seguir waypoints e o fato do UGV ter Ackermann steering.

3.12 Nó de GPS

Foi desenvolvido um nó ROS customizado para o envio de waypoints com base em

coordenadas de GPS. O nó recebe como entrada um conjunto de coordenadas no sistema de

referência geodésico WGS84, que é o padrão para GPS (UNITED NATIONS OFFICE FOR

OUTER SPACE AFFAIRS, 2012), tendo como objetivo traduzir os pontos recebidos para o

sistema de coordenadas local gerado pelo RTAB-MAP e publicá-los como waypoints no NAV

2.

Uma das dificuldades enfrentadas foi traduzir o sistema WGS84, que é tridimensional

e com base em ângulos (UNITED NATIONS OFFICE FOR OUTER SPACE AFFAIRS, 2012),

a um sistema de coordenadas bidimensional e cartesiano, como o Occupancy Grid gerado pelo

RTAB-MAP. Para resolver essa questão foi utilizado o Sistema Universal Transversa de

Mercator (UTM) como intermediário.

Figura 42 – Zonas UTM na América do Sul

O sistema UTM se baseia na projeção de Mercator para tratar a Terra como um plano.

Esse sistema também divide o planisfério em 60 zonas, representando uma a posição qualquer

como a distância entre o ponto até a origem de sua zona (UNITED STATES GEOLOGICAL

SURVEY, 2001). Assim, é possível obter uma representação cartesiana do globo terrestre,

considerando os sentidos norte e leste como positivos para os seus eixos.

Com isso em mente, foi utilizada a biblioteca ROS Geodesy para traduzir as

coordenadas de WGS84 para UTM. Outro desafio encontrado foi a falta de suporte para essa

biblioteca no hemisfério sul. Para o hemisfério norte, o sistema UTM considera o equador como

posição zero do sentido norte, alcançando valores maiores conforme mais ao norte (UNITED

STATES GEOLOGICAL SURVEY, 2001). Já para o hemisfério sul, o UTM considera o

equador como posição 10.000.000, sendo que os valores diminuem conforme mais ao sul

(UNITED STATES GEOLOGICAL SURVEY, 2001). Portanto, foi necessário corrigir os

valores obtidos manualmente, somando 10.000.000 a direção norte calculada pela biblioteca.

Em seguida o nó usa os dados de transformação geométrica providenciados pelo nó

navsat_transform e converte o sistema de referência UTM para o sistema local gerado pelo

RTAB-MAP, com auxílio do pacote ROS TF 2 que interage com transformações geométricas.

Por fim, os pontos são publicados como waypoints para o NAV 2.

3.13 Ajustes do controlador do OSR para seguir padrões do NAV 2

O NAV 2 usa um padrão de mensagem ROS para comandos de velocidade. A

framework envia mensagens do tipo Twist, com as componentes da velocidade divididas nos

eixos x, y e z, tanto em componentes angulares quanto lineares (GEOMETRY_MSGS, 2020).

Entretanto, esse comportamento não coincide com o padrão do projeto OSR original, que usa a

velocidade de pitch (angular em Y) para rotação in-place e a de yaw (angular em Z) para o modo

de Ackermann drive. Essa opção era feita no OSR para facilitar a transmissão de dados pelo

controle remoto, atribuindo um eixo do joystick para cada tipo de rotação (NASA JPL, 2023).

Além disso, a orientação do UGV no eixo X estava invertida na iteração anterior.

Para corrigir essas questões foi necessário realizar alterações no arquivo rover.py do

pacote osr-rover-code, que lida com respostas para comandos de velocidade. Para essa correção

foi necessário inverter o sinal das velocidades e de algumas variáveis responsáveis pela

determinação do ângulo das rodas. O sinal dos valores de escala para os eixos do controle

remoto da iteração anterior também foi alterado para permitir compatibilidade com a iteração

atual.

Além disso, a plataforma OSR espera o uso de motores servo com faixa de movimento

de 300° (NASA JPL, 2023). Os motores utilizados na iteração anterior são de 180°, por isso

também foram atualizados no pacote os dados relativos essa mudança.

3.14 Configuração do NAV 2

A framework NAV 2 permite fazer a configuração de seus plugins com o uso de

arquivos YAML, passados como parâmetros nos arquivos de launch. Os principais plugins do

NAV 2 que foram configurados são: servidor de planejamento de rotas globais, servidor de

controle de trajetórias locais e servidor de comportamento.

Como servidor de planejamento de rota global, foram utilizados em testes as seguintes

opções: Smac Hybrid-A* e NavFn. Percebeu-se que as trajetórias do Smac Hybrid-A* tendiam

a fazer movimentos circulares complexos para situações que podiam ser tratadas mais

facilmente com rotações in-place ou ajustes leves na velocidade angular. Já o planejador NavFn

apresentava trajetos mais simples de serem efetuados, apesar de depender mais do controlador

de trajetórias local dado que não garante rotas cinematicamente factíveis (NAV2, 2023). Optou-

se por escolher o planejador NavFn.

Já em relação aos controladores de trajetória local, foram utilizadas as seguintes opções:

Regulated Pure Pursuit, DWB e Graceful. Um fator que influenciou consideravelmente na

escolha dos controladores foram as restrições de velocidade. Tanto o Regulated Pure Pursuit

quanto o Graceful, usavam contas internas para a definição da velocidade angular que

dificultavam encontrar um valor razoável. Ocorriam casos de envio de comandos de

velocidades desprezíveis que impossibilitavam a movimentação do robô, ou de velocidades

altas ao ponto de o UGV perder referência de odometria. Nessa questão, o controlador DWB é

mais direto, com parâmetros específicos para a definição de velocidades. Optou-se pelo

controlador DWB como opção final.

Por fim, o servidor de comportamento, responsável pelos comportamentos de

recuperação que são acionados caso o UGV seja impossibilitado de seguir sua rota, foi

configurado. A principal problemática desse plugin também é relacionada ao envio de

comandos de velocidade, sendo que o comportamento de recuperação por rotação tem uma

velocidade considerável por padrão, que dificultava a recuperação de odometria.

É possível que os controladores e planejadores que foram rejeitados possam ser

utilizados pela plataforma OSR com uma configuração interna diferente para cada plugin.

Inicialmente foram testadas as configurações recomendadas pelo guia do NAV 2, que

dependem dos tipos de obstáculos e de configurações movimentação do robô, como Differential

drive e Ackermann drive. Nisso foram selecionados, principalmente, a combinação de Smac

Hybrid-A* e Regulated Pure Pursuit (NAV2, 2023).

Entretanto, a plataforma OSR permite tanto o uso de Differential drive quanto de

Ackermann drive, o que abriu as possibilidades de configuração. Além disso, o requisito do

projeto é evitar obstáculos estáticos, sendo que plugins pensados para obstáculos dinâmicos

podem ser configurados para atuarem em ambientes estáticos, o que amplia ainda mais as

possibilidades.

As escolhas feitas pelo grupo se basearam, principalmente, nas configurações padrão do

NAV 2, que utilizam a combinação NavFn e DWB (ROS Navigation, 2023). Essa combinação

apresenta parâmetros mais simples de serem configurados e um resultado satisfatório.

3.15 Proposta de arquitetura em nuvem

Além da estrutura e softwares necessários para navegação autônoma e mapeamento, os

autores deste projeto consideram importante compreender a forma com a qual os dados gerados

pelo robô podem ser usados para gerar informações úteis para os usuários da plataforma. Tendo

isso em mente, foi elaborada uma proposta de arquitetura de solução em nuvem para o projeto,

a partir da qual, uma vez que o robô tenha acesso a rede móvel, seria possível armazenar,

processar e comunicar os dados aos operadores de forma única, sem a necessidade de acesso

direto à rede local do robô ou uso do Rviz.

Entende-se que o acesso a rede móvel pode ser realizado por meio do uso de dispositivos

de tamanho pequeno, como Modems USB ou mesmo receptores portáteis de rede via satélite,

como o Starlink Mini (STARLINK ROAM, 2024), que poderiam ser embarcados diretamente

no robô.


Figura 43 – Arquitetura de solução em nuvem proposta

A arquitetura começa com o próprio robô, que opera como um hub de geração de dados

por meio de dois mecanismos principais: publicação de telemetria e gravação de tópicos

relevantes em arquivos Rosbag. Esses sistemas capturam tudo, desde métricas operacionais

básicas até dados de mapeamento detalhados, criando um rico conjunto de dados que forma a

base de todo o sistema. A integração do robô com o serviço AWS IoT Core serve como ponte

entre as operações de campo e os serviços de nuvem, gerenciando fluxos de dados críticos em

quatro tópicos essenciais: dados de odometria, comandos de velocidade, informações de

localização de GPS e pontos de referência de navegação.

Após os dados entrarem na infraestrutura de nuvem, eles seguem dois caminhos

distintos, mas complementares. O primeiro caminho lida com dados de telemetria em tempo real por meio de um pipeline de pré-processamento que aproveita o serviço Kinesis Data Stream

para ingestão de dados em tempo real e emprega funções sem servidor para processar e

transformar os dados de telemetria em informações acionáveis. Esses dados processados são

então armazenados em um banco de dados de séries temporais usando o Amazon Time Stream,

permitindo consultas e análises eficientes do desempenho histórico do robô. O segundo

caminho gerencia os dados Rosbag mais abrangentes, que são compactados localmente e

armazenados em buckets S3, garantindo que dados operacionais detalhados sejam preservados

para análises futuras e melhorias do sistema.

Dados armazenados em buckets ou em bancos de dados podem ser explorados e

modelados por cientistas de dados em um ambiente colaborativo, por meio de serviços como o

Amazon SageMaker, que permite o desenvolvimento e a implantação de modelos de

aprendizado de máquina, ou o Rekognition, que fornece recursos poderosos de visão

computacional para analisar as condições de campo e a saúde da colheita, por exemplo.

A interface do usuário final, implementada por meio do AWS Amplify, liga a

infraestrutura técnica aos operadores humanos. Essa interface não apenas forneceria recursos

de monitoramento, mas também permitiria o controle remoto e o planejamento de navegação,

possibilitando adaptar as operações do robô em resposta a mudanças nas condições de campo

ou requisitos agrícolas, independente da distância física.

Do ponto de vista operacional, a arquitetura oferece benefícios imediatos por meio da

coleta e processamento automatizados de dados e redução da intervenção manual. No entanto,

seu verdadeiro valor está em seu potencial para gerar insights agrícolas por meio de

monitoramento detalhado de campo, monitoramento da saúde da cultura e análise das condições

ambientais. A relação custo-benefício do sistema é aprimorada por sua utilização otimizada de

recursos e custos de infraestrutura escaláveis, enquanto seu papel como uma plataforma de

inovação fornece oportunidades para implementar recursos avançados de IA/ML e conduzir

pesquisas colaborativas.

No repositório disponível em https://github.com/MekhyW/UGV-Embrapa-Cloud, é

possível encontrar uma base de código, escrita na linguagem HCL e utilizando o framework
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

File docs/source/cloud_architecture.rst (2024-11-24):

Cloud Architecture
===================

During the development of the project, a cloud architecture was proposed to provide the following features:

- Storage of time series telemetry data from the robot.
- Storage of ROSBAG files with rosbags recorded by the robot (including SLAM, image and sensor data).
- Data processing, analysis, modeling and visualization.
- Remote monitoring and control of the robot using a web interface and a localization system.
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

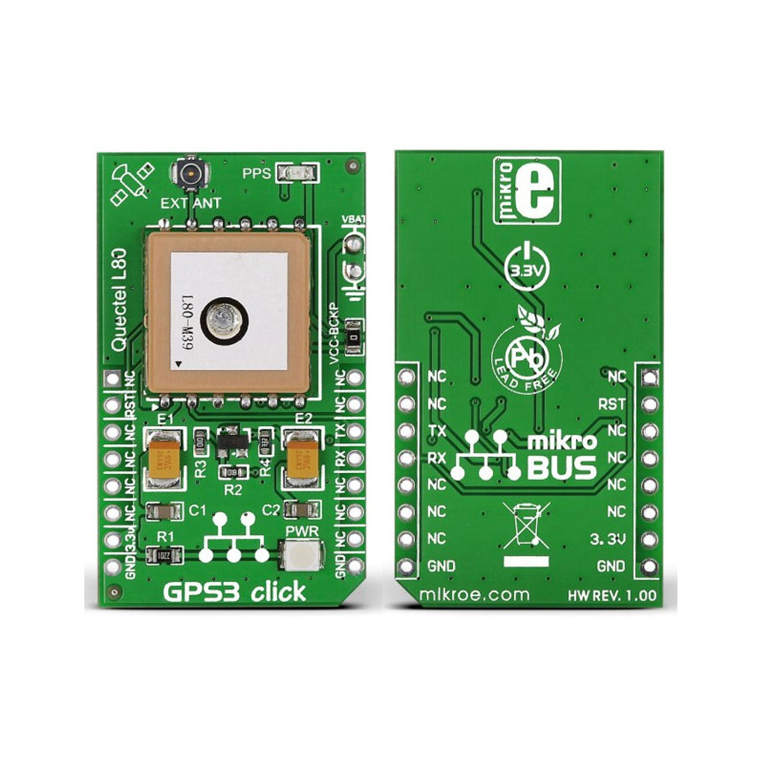
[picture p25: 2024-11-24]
docs/source/_static/gps.jpg

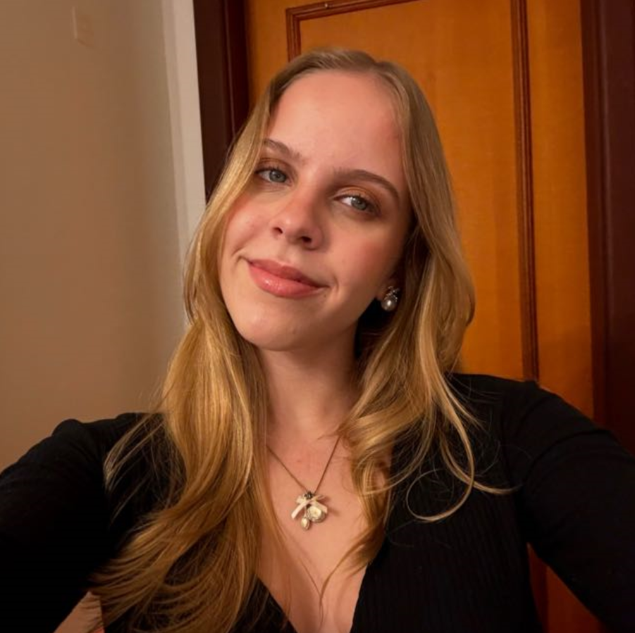
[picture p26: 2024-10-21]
docs/source/_static/luana.png

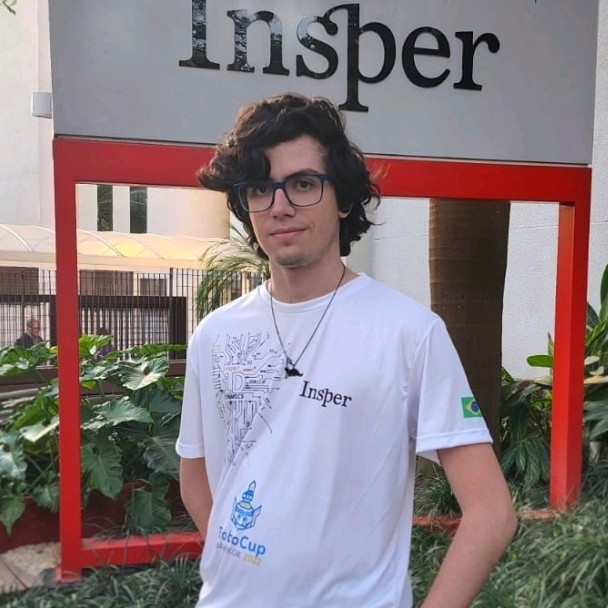
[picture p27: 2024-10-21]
docs/source/_static/felipe.jpg

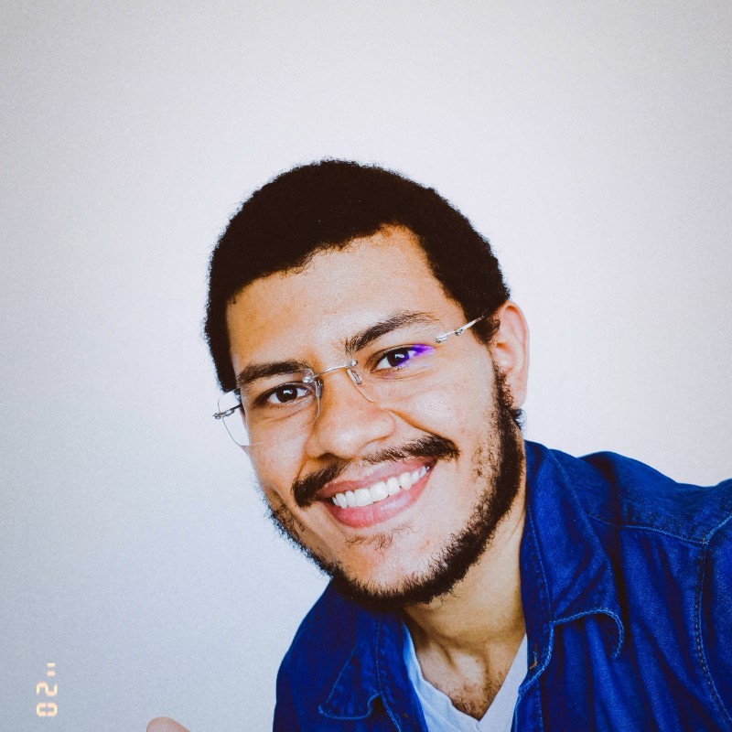
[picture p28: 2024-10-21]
docs/source/_static/breno.jpg

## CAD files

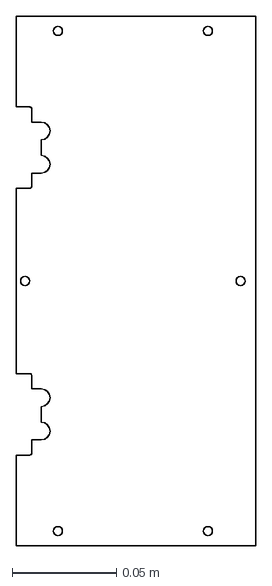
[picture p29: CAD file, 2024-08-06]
Mechanics/dxf acrilico/traseira.dxf
0.115 x 0.254 m

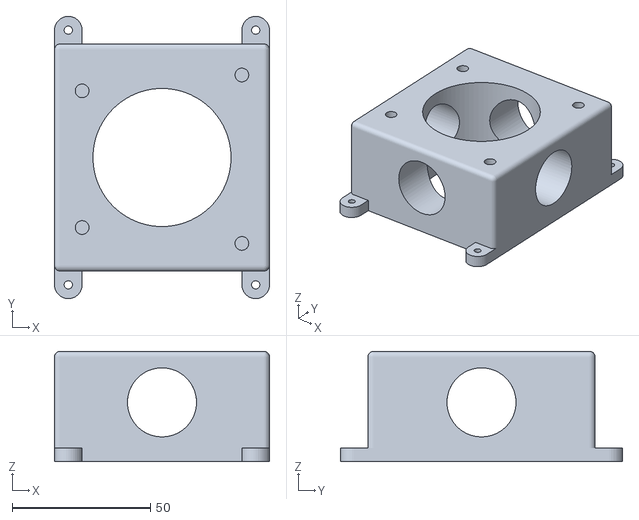
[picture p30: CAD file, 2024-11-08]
Mechanics/Modulo autonomo/Suporte_Lidar.stl
77.9 x 102.2 x 40.0

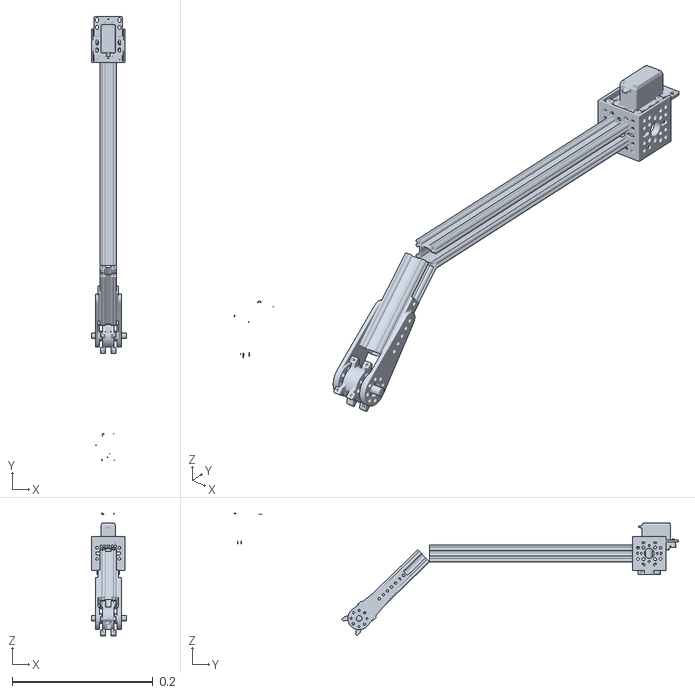
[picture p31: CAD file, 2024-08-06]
Software/osr-rover-code/ROS/osr_gazebo/meshes/rocker_bogie_link_front.stl
0.05 x 0.631 x 0.174

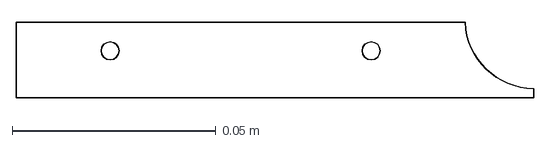
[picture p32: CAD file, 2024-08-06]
Mechanics/dxf acrilico/buraco_superior.dxf
0.127 x 0.0185 m

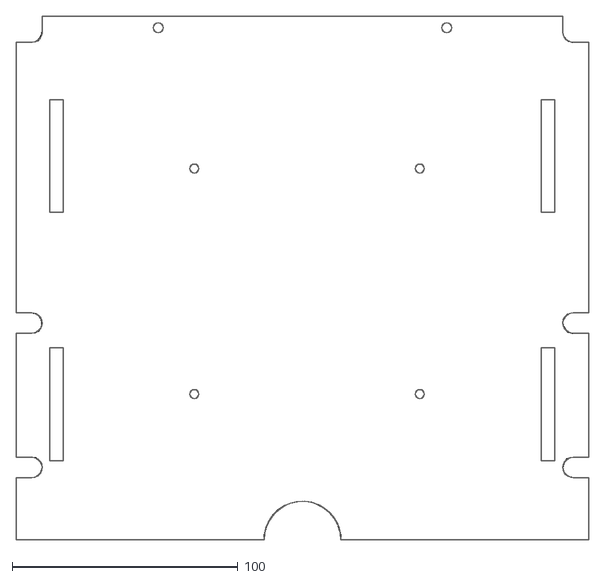
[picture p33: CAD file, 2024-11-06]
Mechanics/Modulo autonomo/topo_oficial_2.dxf
254.0 x 232.0

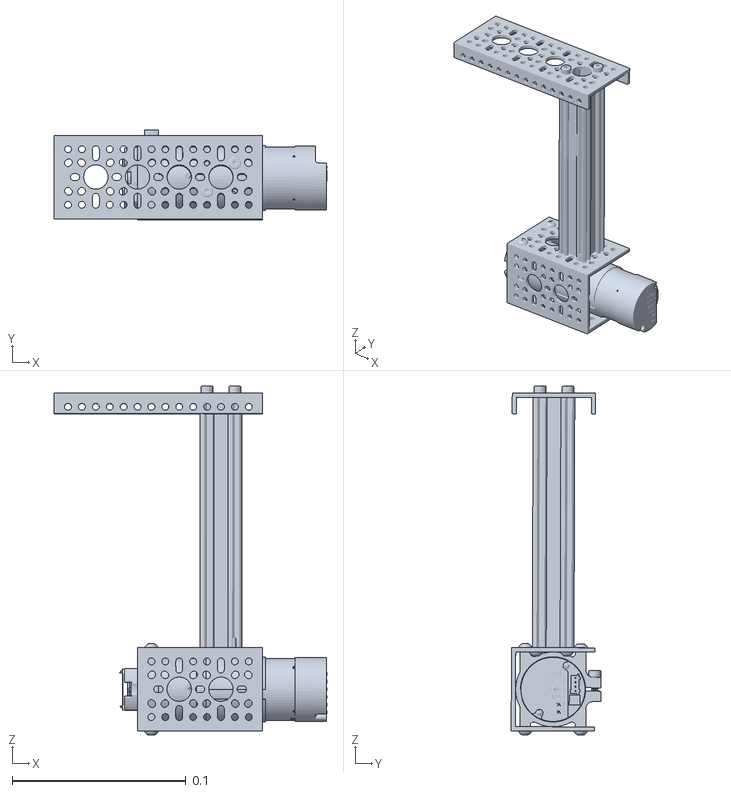
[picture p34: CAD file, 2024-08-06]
Software/osr-rover-code/ROS/osr_gazebo/meshes/wheel_link_left_2.stl
0.157 x 0.0516 x 0.201

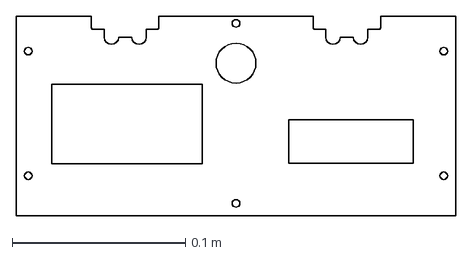
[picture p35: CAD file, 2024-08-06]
Mechanics/dxf acrilico/frente.dxf
0.254 x 0.115 m

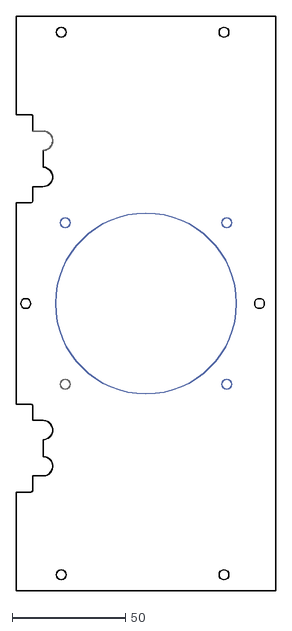
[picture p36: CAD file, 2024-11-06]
Mechanics/Modulo autonomo/tras_nova.dxf
115.0 x 254.0

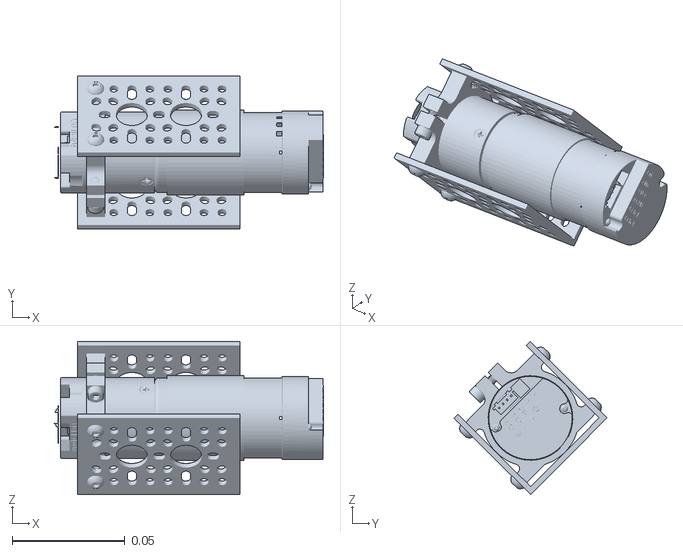
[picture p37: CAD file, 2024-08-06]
Software/osr-rover-code/ROS/osr_gazebo/meshes/wheel_middle_left.stl
0.119 x 0.0679 x 0.0679

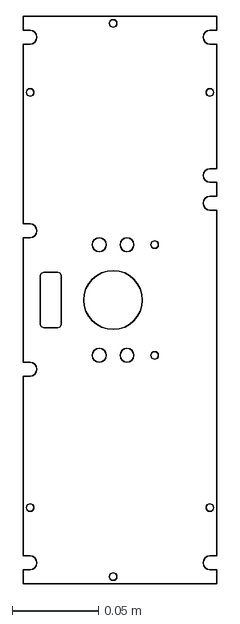
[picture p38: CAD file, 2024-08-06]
Mechanics/dxf acrilico/lado.dxf
0.112 x 0.328 m

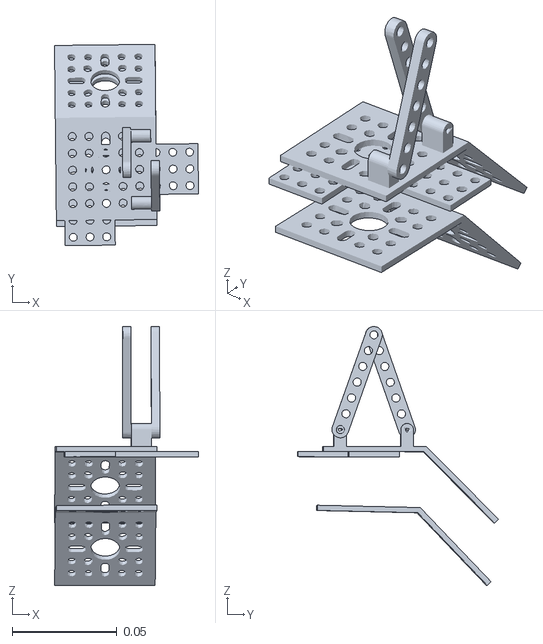
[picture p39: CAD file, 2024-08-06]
Software/osr-rover-code/ROS/osr_gazebo/meshes/turn_left_test.stl
0.0688 x 0.0961 x 0.124

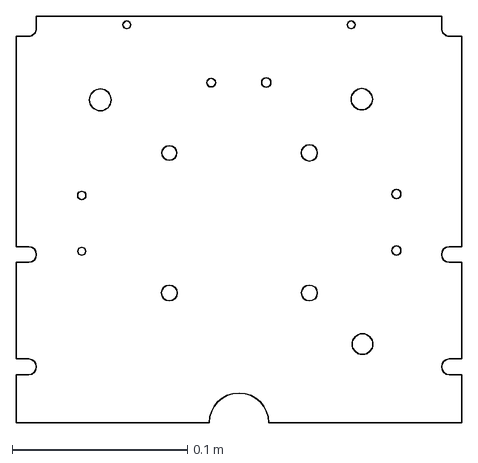
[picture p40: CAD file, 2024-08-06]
Mechanics/dxf acrilico/topo_tras.dxf
0.254 x 0.232 m

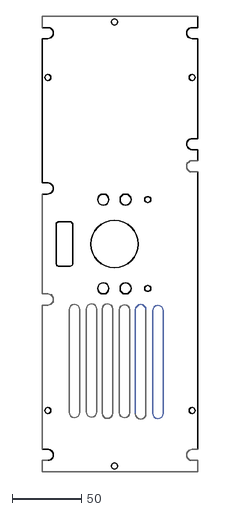
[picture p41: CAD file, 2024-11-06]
Mechanics/Modulo autonomo/laterais_novas.dxf
112.0 x 328.0

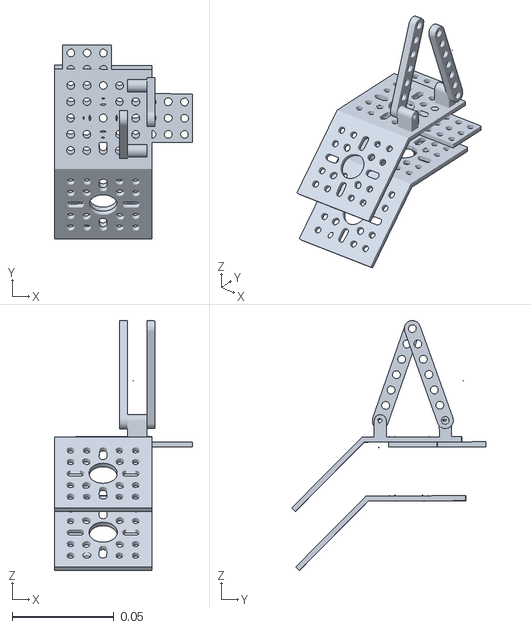
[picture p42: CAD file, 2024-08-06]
Software/osr-rover-code/ROS/osr_gazebo/meshes/turn_right_test.stl
0.0681 x 0.0957 x 0.123

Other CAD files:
Mechanics/Modulo autonomo/topo2.dxf
Mechanics/dxf acrilico/base.dxf
Mechanics/Modulo autonomo/laterais.dxf
Software/osr-rover-code/ROS/osr_gazebo/meshes/arm.stl
Mechanics/Modelagem 3D acrilico/base.f3d
Mechanics/Modelagem 3D acrilico/buraco_superior.f3d
Mechanics/Modelagem 3D acrilico/frente.f3d
Mechanics/Modelagem 3D acrilico/lado.f3d
Mechanics/Modelagem 3D acrilico/topo_frente.f3d
Mechanics/Modelagem 3D acrilico/topo_tras.f3d
Mechanics/Modelagem 3D acrilico/traseira.f3d
Mechanics/Modulo autonomo/caixa.prt
Mechanics/Modulo autonomo/laterais.prt
Mechanics/Modulo autonomo/laterais_novas.prt
Mechanics/Modulo autonomo/suporte_camera_base.f3d
Mechanics/Modulo autonomo/suporte_camera_fixador.f3d
Mechanics/Modulo autonomo/suportes_opti.prt
Mechanics/Modulo autonomo/topo_oficial.prt
Mechanics/Modulo autonomo/tras_nova.prt
Mechanics/dxf acrilico/topo_frente.dxf
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

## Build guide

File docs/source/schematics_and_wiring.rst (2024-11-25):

Schematics and Wiring
=====================

Prerequisites
--------------
The prototype's electronics are made up of two boards: the motor drive board (Motor Board), where the power circuits are located, and the board responsible for controlling the entire system's operation (Brain Board), where the control circuits are located and a Raspberry Pi 4, model B, 8 GB, with a 64-bit quad-core ARM-Cortex A72 microprocessor, running at 1.5 GHz, is located.

The main electronics are based on the original platform schematics found at https://github.com/nasa-jpl/open-source-rover/blob/master/electrical/pcb/control_board/documentation/v2.0.1/schematics.pdf, and the following diagrams:

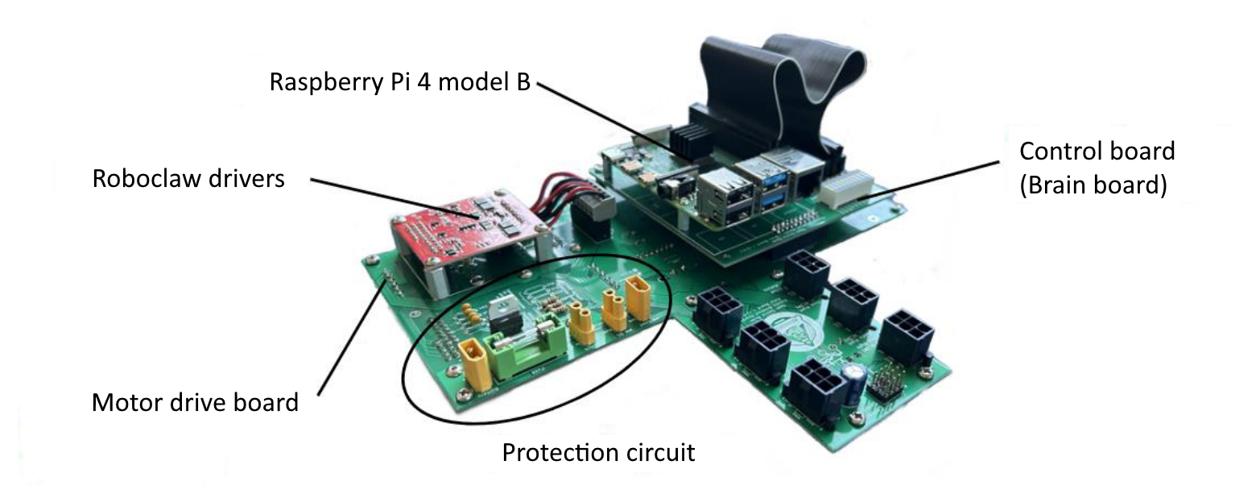
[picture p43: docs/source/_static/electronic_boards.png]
Electronic boards


   Electronic boards.

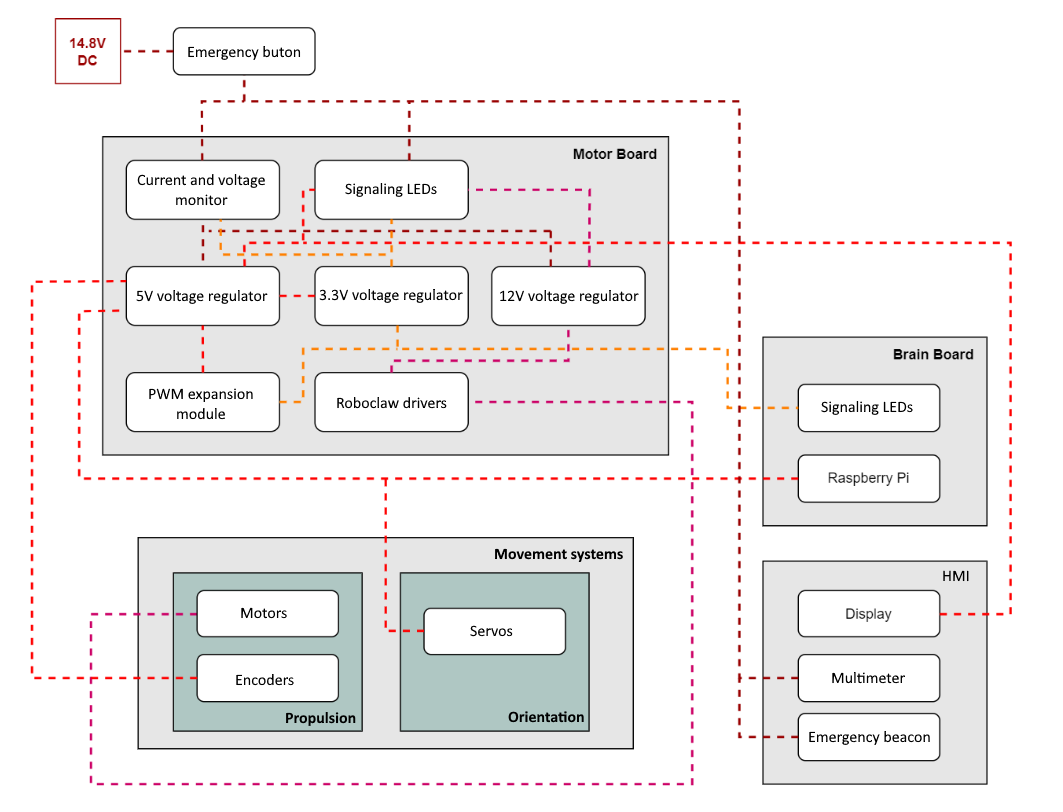
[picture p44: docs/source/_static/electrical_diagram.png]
Electrical diagram


   Electrical diagram.

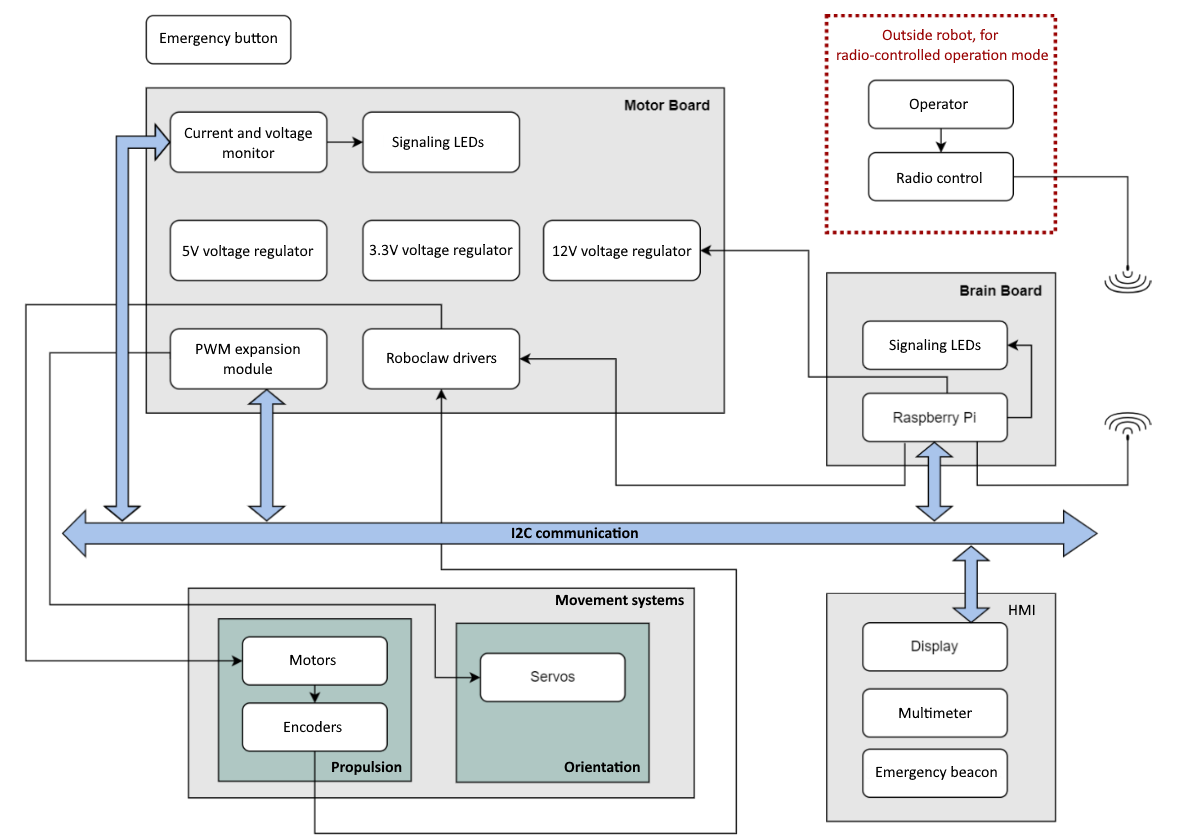
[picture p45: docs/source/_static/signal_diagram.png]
Signal diagram


   Signal diagram.

Power Supply Setup
----------------------
a) Battery Configuration
   
   - Use a 14.8V DC battery
   
   - Connect through protection circuit containing:
        
        * Fuse
        * 1 kΩ resistor
        * Protection diode

b) Voltage Regulation System
   
   - Install voltage regulators:
    
        * 14.8V → 12V (D24V22Fx) for Roboclaw drivers
        * 14.8V → 5V (D24V150Fx) for main systems
        * 5V → 3.3V (MIC2937A-3.3WT) for low-power components

c) Power Distribution

   12V powers:

   - Roboclaw motor drivers

   5V powers:
   
   - Raspberry Pi
   
   - PWM expansion module
   
   - Servo motors
   
   - HMI display
   
   - Motor encoders

   3.3V powers:
   
   - PWM expansion (PCA9685)
   
   - INA260 monitor
   
   - Status LEDs

Motor System Installation
----------------------------

There are two different types of motors being used: brushed DC motors, used to propel the system, and servos, used to change the robot's orientation.

The DC motors are the “5203 Series Yellow Jacket Planetary Gear Motor” model, manufactured by GoBilda, and have a maximum torque of 38 kg.cm. A total of 6 motors are used to move the robot, each equipped with a magnetic encoder, which performs the reading through a hall effect sensor. These readings can be monitored in a specific node, ‘roboclaw_movemotor.py’, contained in: osr-rover-code/scripts/ in the repository of only the robot codes.

The servo motors used are the “Dsservo DS3225” model and have a maximum torque of 21 kg.cm with the 5 V supplied by the drive board. In total, 4 actuators of this type are required to control the robot's orientation, enabling lateral dynamics.

.. warning::
   The servo motors used do not have the same range of rotation as the ones from the original NASA design (180 instead of the original 300 degrees). This required changes to the control system to adapt to the new range.

a) DC Motors
   
   - Install 6x GoBilda 5203 Series Yellow Jacket Planetary Gear Motors
   
   - Specifications: 38 kg.cm maximum torque
   
   - Connect magnetic encoders to each motor
   
   - Wire to Roboclaw drivers

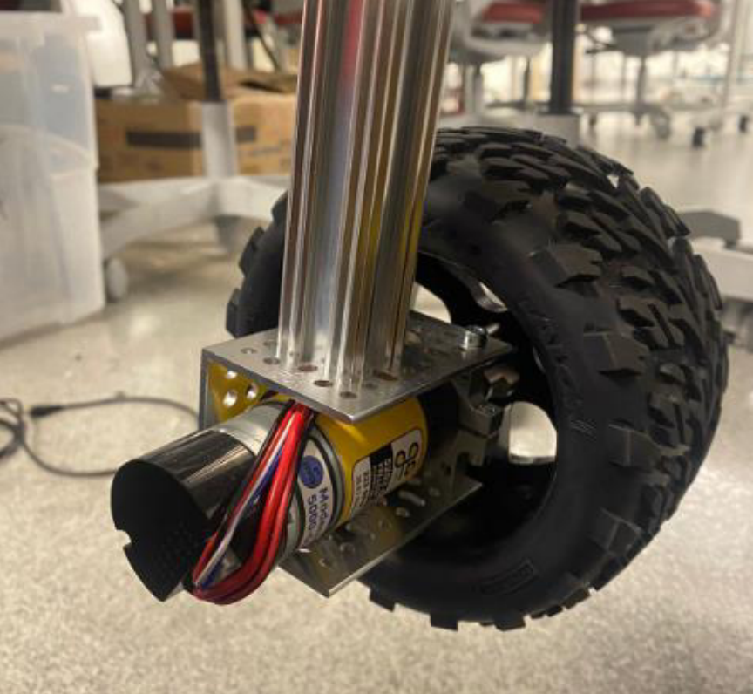
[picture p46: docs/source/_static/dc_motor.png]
DC motor


   DC motor.

b) Servo Motors
   
   - Install 4x Dsservo DS3225
   
   - Specifications: 21 kg.cm at 5V
   
   - Connect to PCA9685 PWM expansion module

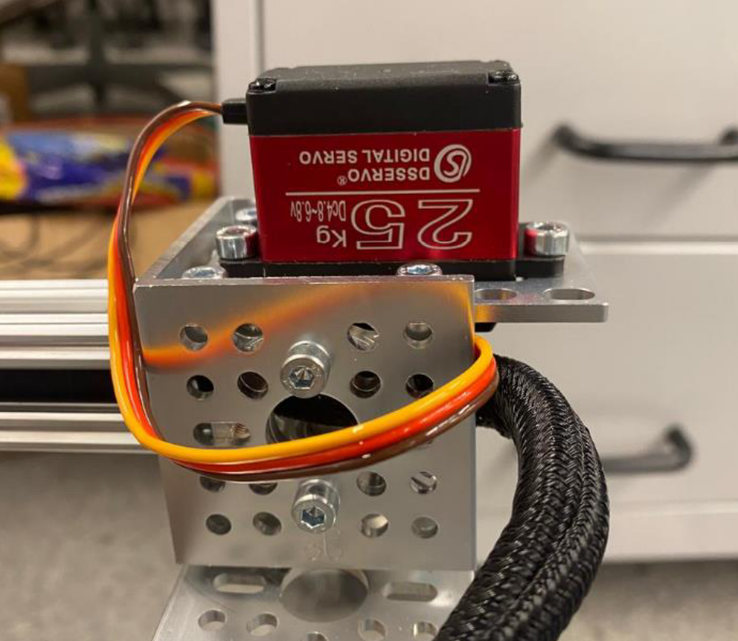
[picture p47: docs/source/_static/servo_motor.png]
Servo motor


   Servo motor.

Control Systems Setup
----------------------
Considering the communication between the microcomputer and the voltage and current monitoring module (INA260), it is noted that data is also sent via an I2C communication protocol. The module also communicates with the signaling LEDs to alert the user if its internal shunt resistor detects any change in the power supply system.

a) PWM Control
   
   - Install PCA9685 module
   
   - Connect to Raspberry Pi via I2C
   
   - Wire 16 PWM channels as needed

In addition to the expansion module and the monitor, communication with the HMI display, which will be implemented in the future, will also take place using the I2C protocol. The reason for this choice is that the control board has an available I2C bus, which could be adapted for connecting the display with a low number of adaptations required.

Another important observation regarding the diagram is that the Raspberry Pi is also responsible for controlling the 12V voltage regulator through an enable signal, turning the 12V output on or off.

Analyzing the control board a little more, we can see the presence of some signaling LEDs. These components are intended to communicate with the user, signaling, for example, when data is being transferred via the serial port, lighting up when the bits are transferred.

b) Monitoring System
   
   - Install INA260 module
   
   - Connect via I2C to Raspberry Pi
   
   - Wire status LEDs for power monitoring

Safety Systems
---------------
To ensure the prototype's compliance with the occupational safety standard for machines and equipment (NR-12), it was necessary to include an emergency circuit, containing a physical emergency button and ensuring the robot's complete stop, in addition to de-energizing the control and power boards, through a normally closed switch, responsible for cutting off the power supplied to both boards.

a) Emergency Circuit
   
   - Install physical emergency button (NC switch)
   
   - Wire to power cutoff system for both boards
   
   - Configure remote emergency via radio control

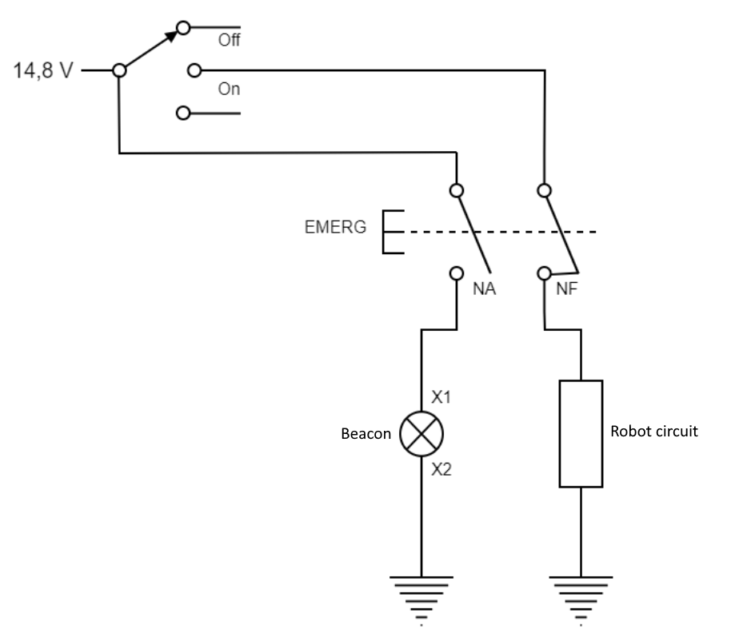
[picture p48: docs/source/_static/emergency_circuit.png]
Emergency circuit


   Emergency circuit.

b) Status Indicators
   - Install status LEDs for:
        
        * Serial communication
        
        * Power status
        
        * Emergency status

Display Installation
---------------------
To display relevant information about the robot's status, such as connectivity, battery percentage, etc., a 16x02 LCD display with an I²C conversion module was installed, as provided in the project's solution matrix. It was necessary to supply it with 5V on one of the available power pins indicated by the brain board's silkscreen, as well as connect the SDA and SCL pins.

- Install 16x02 LCD display with I²C module

- Connect to 5V power

- Wire SDA and SCL pins to Raspberry Pi

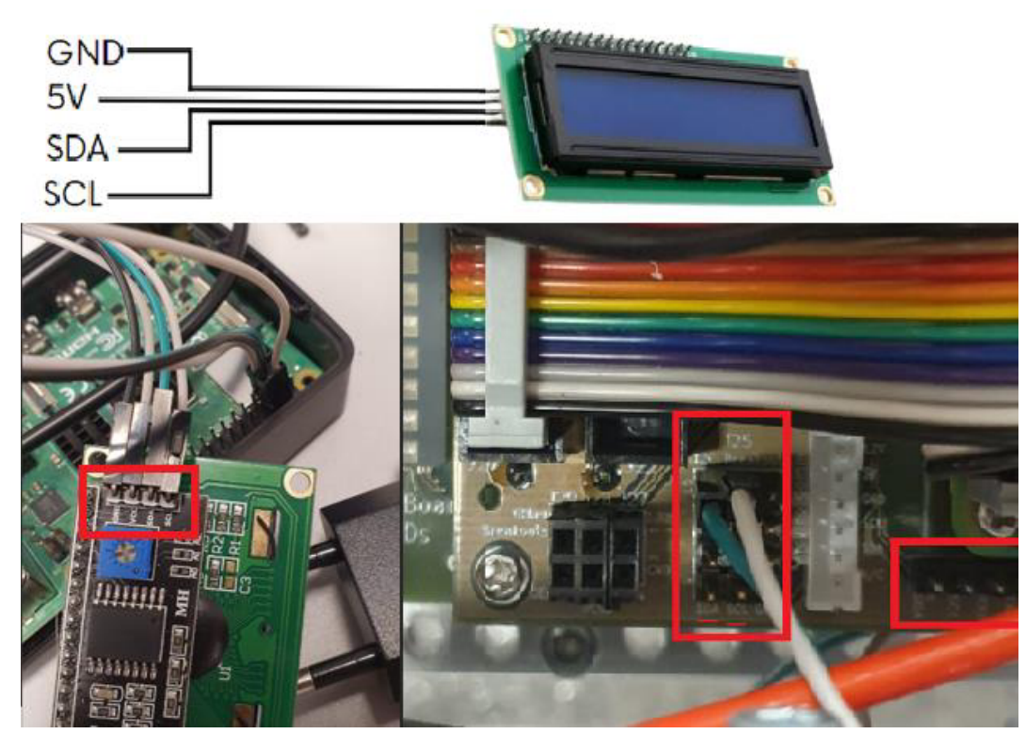
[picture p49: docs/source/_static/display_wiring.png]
Display wiring


   Display wiring.

Wiring Guidelines
------------------
The wiring required for power supply, encoder reading and signal transmission to the actuators followed the instructions in the GitHub repository at: https://github.com/nasa-jpl/open-source-rover/tree/master/electrical/wiring. The suggested dimensions, however, were reduced, so an excess of at least 10 cm was added to each wire. The color code was respected as well as the gauge of the motor power wires. Wires for control signals were replaced with smaller AWG gauge two-piece.

- Add 10cm extra length to all specified wire lengths

- Follow color coding scheme

- Use specified AWG for motor power

- Use smaller AWG for control signals

Dell Optiplex Power Supply
--------------------------

In order to use the Optiplex 7000MFF, a power supply circuit responsible for adjusting the battery voltage from 14.8V to the computer's input voltage of 19.5V is necessary. 

This is accomplished using a step-up voltage regulator, which takes advantage of the available components on the motherboard and the power supply circuit, and is installed after the fuse and multimeter.

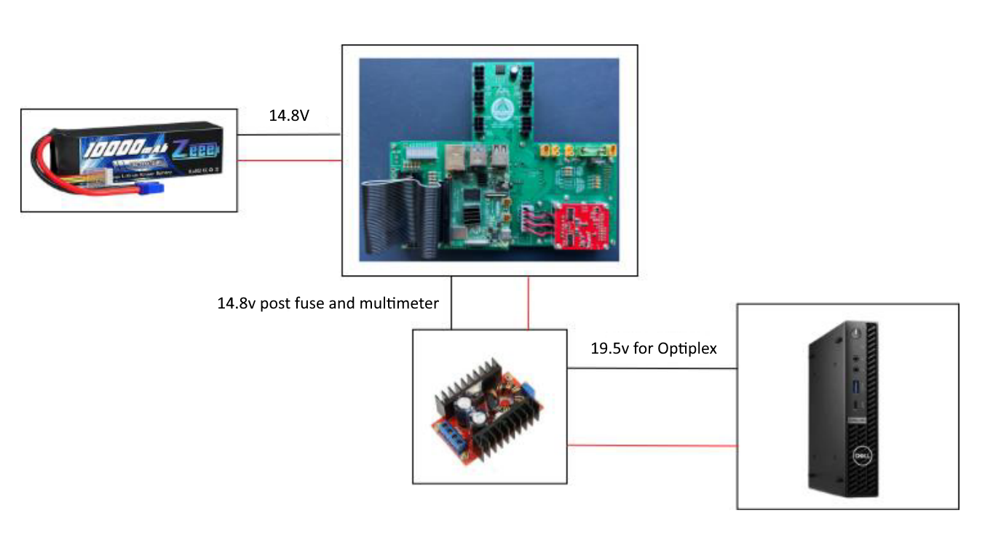
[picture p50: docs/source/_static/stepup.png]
Diagram of the step-up voltage regulator


   Diagram of the step-up voltage regulator.

The regulator module can potentially reach dangerous temperatures if not properly isolated from the surrounding components and cooled. In order to test the power regulator for efficiency and thermal performance, the following test circuit can be used:

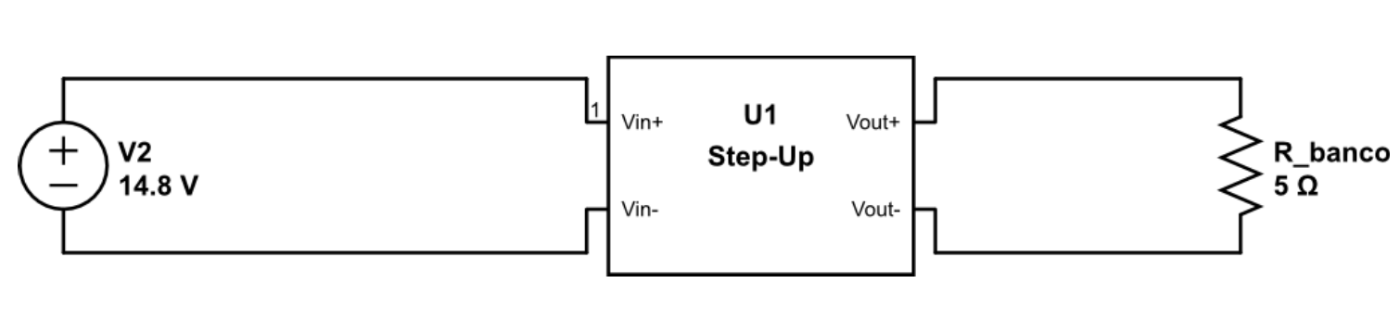
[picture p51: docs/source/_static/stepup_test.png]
Test circuit for the power regulator


   Test circuit for the power regulator.

GPS Module Board
------------------

The GPS module board integrates a NEO-6M GPS module with a TTL to USB converter. The board can be manufactured using the provided KiCad design files located in the Electronics/GPS directory.

a) Manufacturing Files
  
  The following files are required for PCB fabrication:
  
  - Circuit design: GPS.kicad_sch
  - PCB layout: GPS.kicad_pcb
  - Drill files:
       * FabOutput/Gerber/GPS-NPTH.drl (Non-plated holes)
       * FabOutput/Gerber/GPS-PTH.drl (Plated holes)
       * FabOutput/Drill/GPS-NPTH.drl (Non-plated holes backup)
       * FabOutput/Drill/GPS-PTH.drl (Plated holes backup)

b) Manufacturing Specifications
  
  - Board material: FR4
  - Layers: 2
  - Thickness: 1.6mm
  - Copper weight: 1oz
  - Surface finish: HASL (lead-free)
  - Solder mask: Green
  - Silkscreen: White

c) Assembly Instructions
  
  1. Order PCB fabrication using provided Gerber and drill files
  2. Solder components in the following order:
       * TTL to USB converter
       * Power regulation components
       * GPS module socket
       * Pin headers
  3. Install GPS module into socket
  4. Verify all connections with multimeter before powering

d) Testing
  
  - Check voltage levels at power test points
  - Verify USB enumeration when connected
  - Test GPS signal acquisition in open area
  - Confirm serial communication at 9600 baud

.. note::
  The board design includes protection circuitry and proper power regulation for reliable operation.

Testing and Verification
------------------------
- Test voltage levels at all regulation points

- Verify emergency shutdown functionality

- Test motor control systems

- Confirm encoder readings using roboclaw_movemotor.py

- Verify I2C communication with all peripherals

.. note::
   Always refer to the original schematics for detailed connection diagrams and component specifications.

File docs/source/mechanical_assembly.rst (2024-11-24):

Mechanical Assembly
===================

Overview
--------

The robot's structure is an adaptation of unmanned vehicles that monitor the surface of Mars and the moon. It features a Rocker-Bogie suspension made of aluminum profile, developed in 1996 for NASA's Sojourner rover. This suspension system keeps the chassis level even on uneven terrain, minimizing rolling and pitching.

The suspension consists of two axles:

1. The first axle is fixed to the chassis and rotates the larger arm (rocker).
2. The second axle is at the end of the first and rotates the smaller arm (bogie).

Wires from the motors and encoders pass through these axles to the inside of the chassis.

Chassis Design
--------------

The robot's chassis is composed of:

- Aluminum bars
- Acrylic sheets

These components house the device's electronic boards, batteries, and HMI. Camera and LiDAR supports are attached to the chassis.

Design Considerations:

- The robot's center of mass is positioned above the unsprung mass (wheels and suspension) for greater stability.
- Maximum incline is limited to angles less than 45° due to the height of the center of mass.
- Obstacles exceeding the combined torque of the six motors or with a height greater than the wheel radius cannot be overcome.

Assembly Instructions
---------------------

**For detailed instructions on base assembly, including the main body frame and rocker-bogie suspension, refer to the Open Source Rover official docs:** https://github.com/nasa-jpl/open-source-rover/tree/master/mechanical.

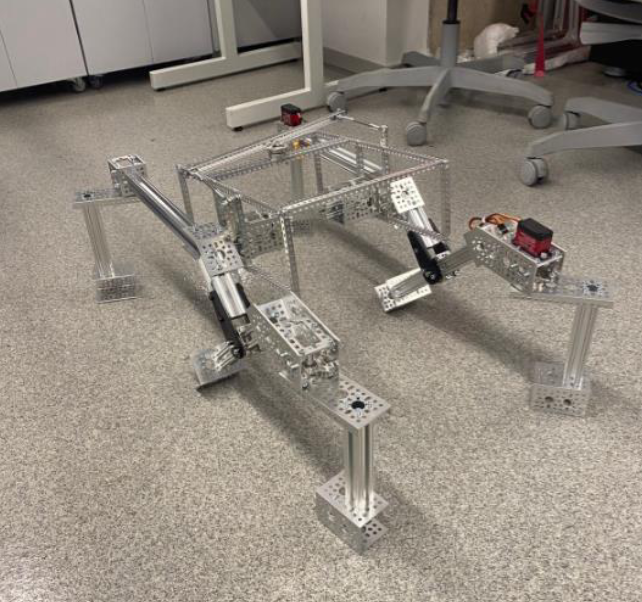
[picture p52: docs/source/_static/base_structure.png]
Base structure


   Base structure.

- Wheel assembly subsystem: https://github.com/nasa-jpl/open-source-rover/blob/master/mechanical/wheel_assembly/README.md

- Main body subsystem: https://github.com/nasa-jpl/open-source-rover/blob/master/mechanical/body/README.md

- Rocker-Bogie suspension subsystem: https://github.com/nasa-jpl/open-source-rover/blob/master/mechanical/rocker_bogie/README.md

Component Adaptations
---------------------

Some parts may need adaptation based on component availability:

Aluminum Profiles
^^^^^^^^^^^^^^^^^

If 96 mm profiles are unavailable:

1. Purchase larger profiles and cut to the correct dimension.
2. Redo threading for M4 screws in all four holes of each cut part.
3. Use taps of different sizes in three stages to achieve the desired thread size.

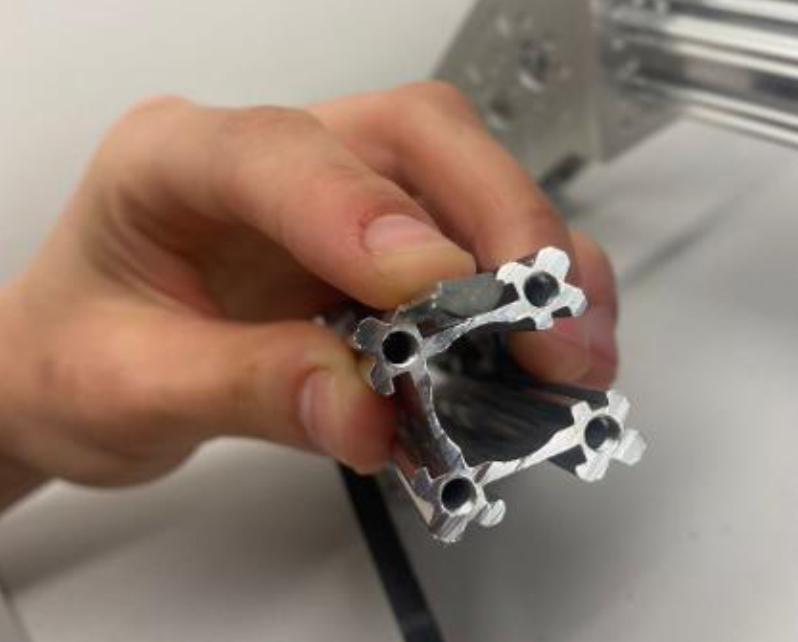
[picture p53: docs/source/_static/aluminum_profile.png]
Aluminum profile


   Cut aluminum profile.

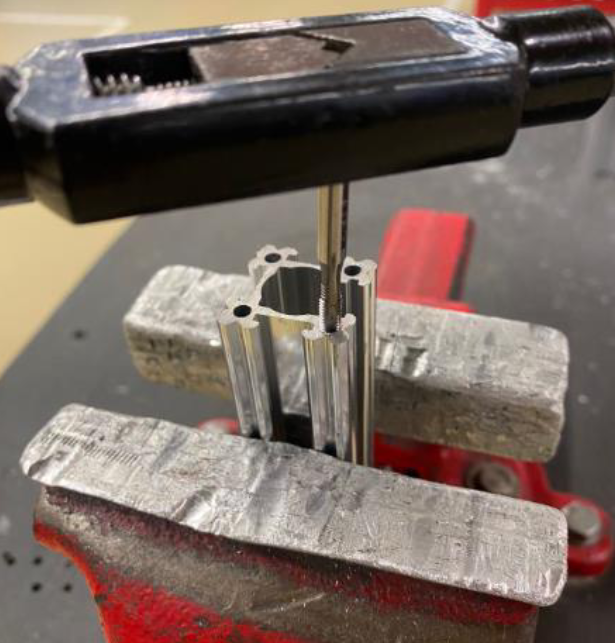
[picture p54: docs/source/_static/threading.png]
Threading


   Threading operation.

Drilling Operations
^^^^^^^^^^^^^^^^^^^

After cutting the parts, it may be necessary to drill the bars, since the existing hole may not be through like in the profile. In addition, it may also be necessary to perform threading in two stages, as was the case with the other part mentioned above.

If drilling is necessary, follow these steps:

1. Paint the face to be drilled with a marker.
2. Mark the hole center using a vertical height marker.
3. Create a central mark using a center punch, vice, and hammer.
4. Drill using a manual benchtop milling machine, ensuring proper alignment and chip evacuation.

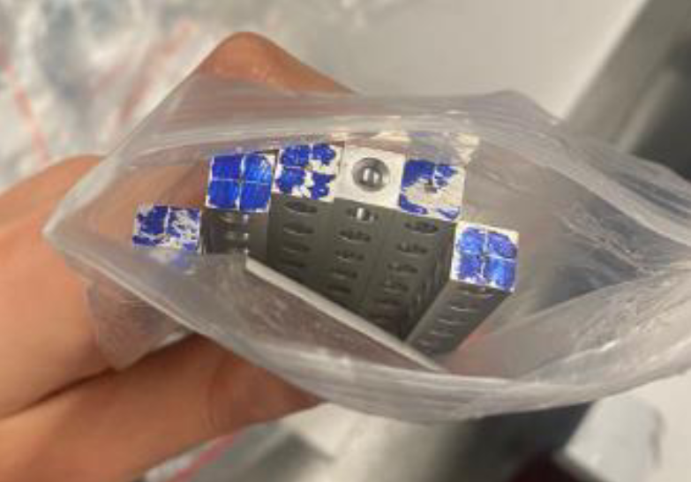
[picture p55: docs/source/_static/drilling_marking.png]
Drilling marking


   Marking for drilling operation.

Bearing Substitution
^^^^^^^^^^^^^^^^^^^^

If the original bearing part is unavailable:

- Use a substitute with an equivalent internal diameter.
- Note that slight structural deformation may occur but should not compromise operation.

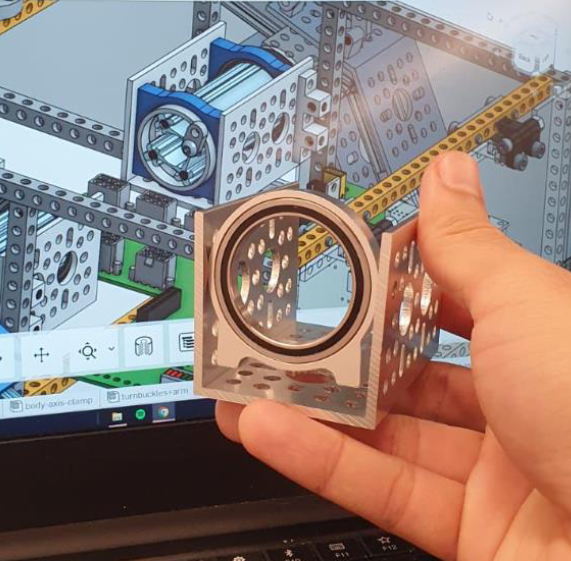
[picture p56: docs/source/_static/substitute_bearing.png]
Substitute bearing


   Substitute bearing.

Wheel Fixation
^^^^^^^^^^^^^^^

Due to the torque of the engines, it may be necessary to modify the wheel attachment.

Originally, the attachment is established between the engine shaft and the wheel with a central screw pressing the wheel between a washer and the wheel hub attached to the engine shaft. After the new attachment, the wheels are drilled and attached, with two screws each, to the wheel hubs. However, it was found that this strategy, suggested in the official project repository, is prone to misalignment.

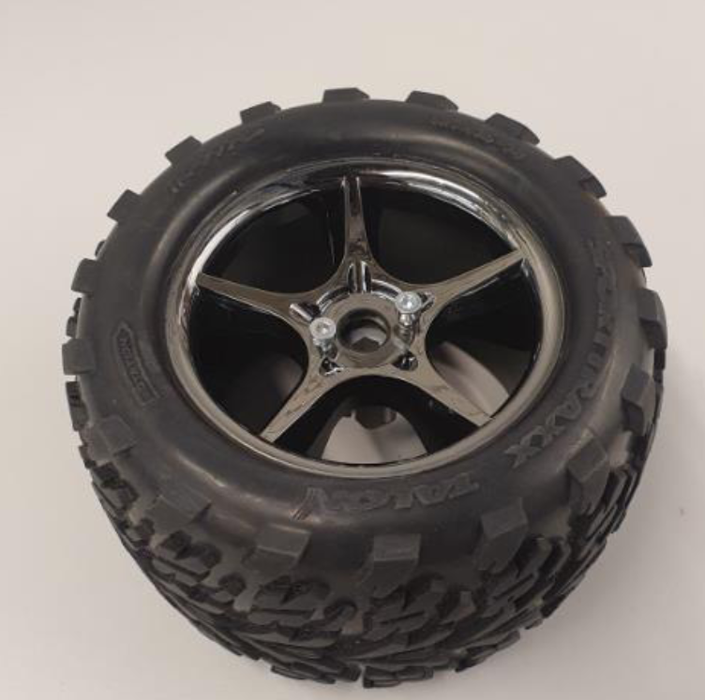
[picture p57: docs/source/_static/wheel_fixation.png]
Wheel fixation


   Example of attaching the wheel to the hub

.. note::
   As of the writing of this document, there is an error in the official documentation:

   - Component initially coded as 1601 actually corresponds to component number 1611.
   - The 3D assembly view shows a part with an internal diameter less than 8 mm, which does not fit the specified axle.

Autonomous Navigation/SLAM Module
---------------------------------

To allow the robot to navigate autonomously, perform SLAM and communicate with the robot's HMI, it is necessary to make the casing that houses the navigation module and supports for the robot's sensors, then mount the navigation module and sensors on the case (on top of the base platform structure).

Acrylic Case
^^^^^^^^^^^^^

Cutting files for the acrylic case, separated into walls, bottom and top, are available in the "Mechanics/Modulo autonomo" folder. The .dxf files can be opened with tools such as RDWorks or Rhino, and .prt files can be opened with tools such as Siemens NX.

It is necessary to use a laser cutting machine to cut the acrylic sheets, then screw the bottom part to the base structure. The top part simply slides in place, above the case walls.

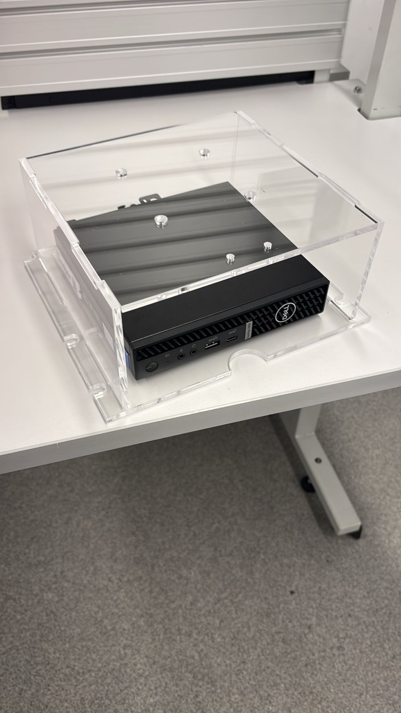
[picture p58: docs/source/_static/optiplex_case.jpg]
Acrylic case


   Acrylic case.

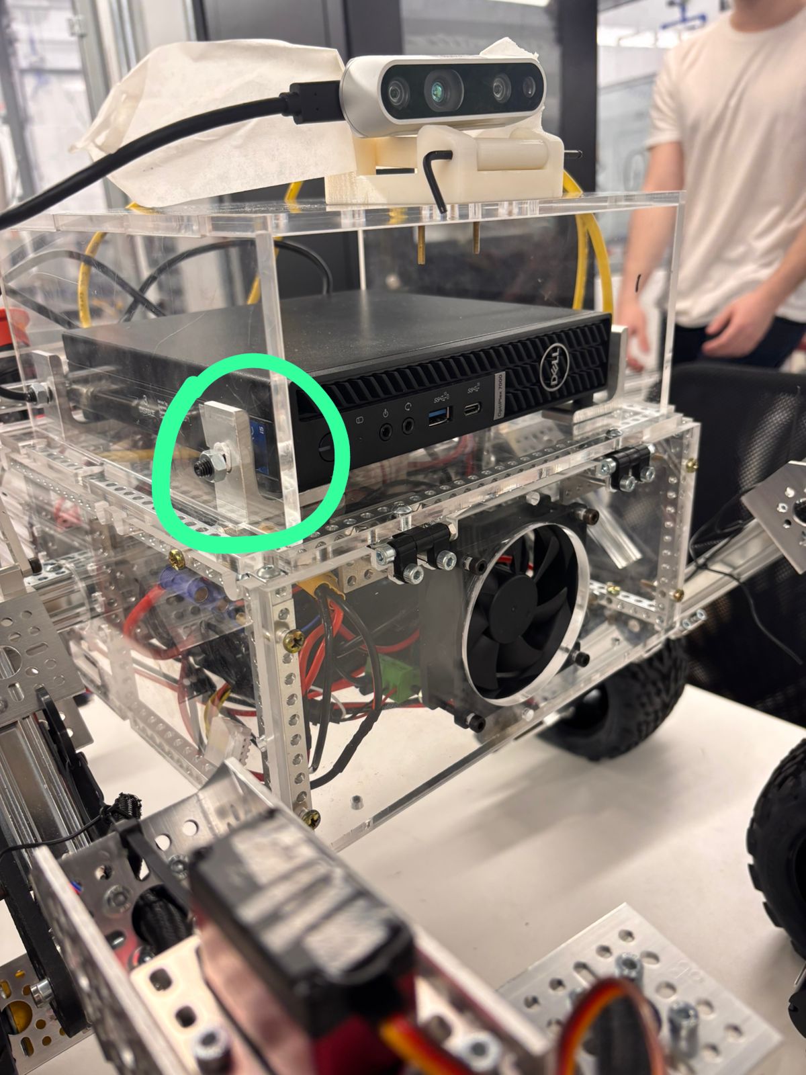
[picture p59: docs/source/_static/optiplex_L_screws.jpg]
L-screws


   L-screws used to fix the bottom part to the base structure.

Cooler Fan Hole
^^^^^^^^^^^^^^^^

A hole is required to intall the cooler fan in front of the step-up converter module, which is used to power the Optiplex board for the navigation module.
To achieve this, a 80mm hole was drilled in the front wall of the chassis, and the fan was fixed via 4x M3 screws and nuts.

Sensor Mounting
^^^^^^^^^^^^^^^^

Printable files for the sensor mounting pieces (both for the RealSense D435i and the LDS02 Lidar) are available in the "Mechanics/Modulo autonomo" folder.

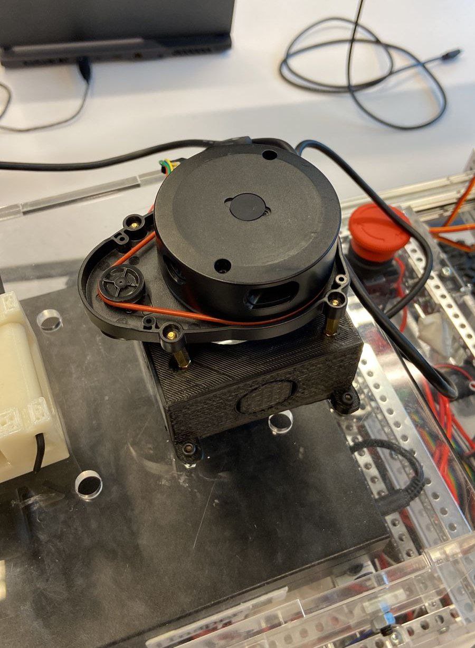
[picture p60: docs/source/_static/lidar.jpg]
Lidar mounting


   Lidar mounting.

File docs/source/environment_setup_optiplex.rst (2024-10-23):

Environment Setup - Dell Optiplex
=================================

This section describes the steps to prepare the development environment for the UGV project on the Dell Optiplex, which is the computing platform for the SLAM/autonomous navigation module. The Optiplex communicates with the Raspberry Pi over Ethernet during operation.

1. Install ROS 2 Humble and Required Packages
---------------------------------------------

Run the following commands to install necessary packages:

.. code-block:: bash

   sudo apt install ros-humble-desktop
   sudo apt install ros-humble-librealsense2*
   sudo apt install ros-humble-realsense2-*
   sudo apt install ros-humble-rtabmap-ros
   sudo apt install ros-humble-imu-tools
   sudo apt install ros-humble-control-msgs

2. Create a Colcon Workspace
----------------------------

Set up a Colcon Workspace to manage ROS packages without official Rosdistro binaries:

.. code-block:: bash

   mkdir -p ~/osr_ws/src
   cd ~/osr_ws/src

3. Clone Required Repositories
------------------------------

Download the following repositories into the `src` folder:

.. code-block:: bash

   git clone https://github.com/ROBOTIS-GIT/ld08_driver.git
   git clone https://github.com/your-username/UGV-Embrapa.git

4. Build the Workspace
----------------------

Build the workspace using Colcon:

.. code-block:: bash

   cd ~/osr_ws
   colcon build --symlink-install
   source ~/osr_ws/install/setup.bash

5. Configure Realsense D435i
----------------------------

Calibrate the IMU of the Realsense D435i camera:

a. Install the pyrealsense2 library:

   .. code-block:: bash

      pip install pyrealsense2

b. Clone the Librealsense repository:

   .. code-block:: bash

      git clone https://github.com/IntelRealSense/librealsense.git
      cd librealsense/tools

c. Run the calibration script:

   .. code-block:: bash

      python3 rs-imu-calibration.py

d. Follow the on-screen instructions to position the camera in 6 different orientations.
   Aim for a calibration grade close to 98 (the achieved grade was 98.05).

6. Configure LiDAR LDS-02
-------------------------

Set up udev rules for the LiDAR:

a. Clone the TurtleBot3 repository (if not already done):

   .. code-block:: bash

      cd ~/osr_ws/src
      git clone https://github.com/ROBOTIS-GIT/turtlebot3.git

b. Copy the udev rules file:

   .. code-block:: bash

      sudo cp ~/osr_ws/src/turtlebot3/turtlebot3_bringup/99-turtlebot3-cdc.rules /etc/udev/rules.d/

c. Reload and trigger udev rules:

   .. code-block:: bash

      sudo udevadm control --reload-rules
      sudo udevadm trigger

7. Final Steps
--------------

Your SLAM/autonomous navigation project environment is now set up. Remember to source the workspace setup file in each new terminal:

.. code-block:: bash

   source ~/osr_ws/install/setup.bash

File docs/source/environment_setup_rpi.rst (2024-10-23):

Environment Setup - Raspberry Pi
================================

This section describes the steps to prepare the development environment for the UGV project on the Raspberry Pi, which is the base board of the robot platform, including the installation of the operating system, ROS 2 Humble, and the configuration of the Raspberry Pi for control.

Operating System Installation
-----------------------------

1. Download Ubuntu Server Image:
   
   - Go to the `official Ubuntu Server website <https://ubuntu.com/download/server>`_ and download the latest image.
   - Use software like Raspberry Pi Imager to save the image to the SD card.

2. Initial Setup:
   
   - Insert the SD card into the Raspberry Pi and turn on the device.
   - Configure Wi-Fi network and other basic preferences during startup.
   - Update the operating system:

     .. code-block:: sh

        sudo apt update
        sudo apt upgrade

Configuring Raspberry Pi as Server and SSH Communication
--------------------------------------------------------

1. Server Mode:
   
   - Server configuration allows Raspberry Pi to be accessed remotely.
   - Connect to the server using SSH:

     .. code-block:: sh

        ssh embrapa@10.42.0.1

ROS Humble Installation
-----------------------

1. Add ROS Repository Key:

   .. code-block:: sh

      sudo apt install software-properties-common
      sudo add-apt-repository universe
      sudo apt update
      sudo apt install curl
      curl -sSL https://raw.githubusercontent.com/ros/rosdistro/master/ros.asc | sudo apt-key add -

2. Add ROS Repository:

   .. code-block:: sh

      sudo sh -c 'echo "deb http://packages.ros.org/ros2/ubuntu $(lsb_release -cs) main" > /etc/apt/sources.list.d/ros2-latest.list'
      sudo apt update
      sudo apt install ros-humble-desktop

3. Configure ROS Environment:
   
   Add the following lines to the ``~/.bashrc`` file:

   .. code-block:: sh

      source /opt/ros/humble/setup.bash

Manual Rover Bringup
--------------------

To manually start the rover, run the following commands in the terminal:

1. Make sure the program is not already running:

   .. code-block:: bash

      sudo systemctl stop osr_startup

2. Execute the bringup command:

   .. code-block:: bash

      ros2 launch osr_bringup osr_launch.py

Automatic Bringup with Launch Script
------------------------------------

To automate the bringup and eliminate the need for SSH access, configure the Raspberry Pi to launch the rover code automatically:

1. Navigate to the ``init_scripts`` folder:

   .. code-block:: bash

      cd ~/osr_ws/src/osr-rover-code/init_scripts

2. Create symbolic links:

   .. code-block:: bash

      sudo ln -s $(pwd)/launch_osr.sh /usr/local/bin/launch_osr.sh
      sudo ln -s $(pwd)/osr_paths.sh /usr/local/bin/osr_paths.sh

3. Copy the service file to the systemd services directory:

   .. code-block:: bash

      sudo cp osr_startup.service /etc/systemd/system/osr_startup.service

4. Adjust service file permissions:

   .. code-block:: bash

      sudo chmod 644 /etc/systemd/system/osr_startup.service

Image Acquisition Setup
-----------------------

1. Installation of Required Libraries:

   .. code-block:: sh

      sudo apt install ros-humble-cv-bridge
      sudo apt install ros-humble-image-transport

2. Camera Configuration:
   
   - Connect Intel RealSense D435i and Logitech C920 HD PRO cameras to Raspberry Pi.
   - Use the following commands to check and adjust settings:

     .. code-block:: sh

        rs-enumerate-devices
        v4l2-ctl --list-devices

3. Publishing and Viewing Images:
   
   - Run ROS nodes to capture and publish images:

     .. code-block:: sh

        ros2 run realsense2_camera realsense2_camera_node
        ros2 run image_transport republish raw in:=/camera/color/image_raw out:=/image_raw

   - Another way to start capturing images:

     .. code-block:: sh

        systemctl restart start_turtle.service

   - To view images use Rviz2 or rqt_image_view:

     .. code-block:: sh

        ros2 run rqt_image_view rqt_image_view
        # or
        rviz2

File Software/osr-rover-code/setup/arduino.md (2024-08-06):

# Flashing the Arduino code

In this section we will be flashing the code that runs on the arduino to control the LED matrix in the head. The following steps should be performed on your laptop or development machine (not the raspberry pi)

1. Install the [Arduino IDE](https://www.arduino.cc/en/Main/Software) used for loading code onto the arduino
2. Download the Arduino code:
    1. Navigate to [the repo](https://github.com/nasa-jpl/osr-rover-code) and click the green "Clone or download"
button. Choose "Download ZIP".
    2. Unzip/extract and open the downloaded zip file. Then, select the Arduino folder and create a
new zip file of just that Arduino folder. Name it OsrScreen.zip
3. Load the sketch onto the Arduino
    1. Unplug the Arduino shield JST cable so the Arduino isn’t powered by the control board
    2. Connect the Arduino to your development machine with USB cable
    3. Open Arduino IDE
    4. Select Sketch -> Include Library -> Add .Zip Library
    5. Select the OsrScreen.zip folder created previously
    6. Click the Upload button in the Sketch Window
4. To load the example in the Arduino IDE: File -> Examples -> OsrScreen -> OsrScreen

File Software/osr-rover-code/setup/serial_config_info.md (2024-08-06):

Configuration can be a bit of a pain for using the serial port on the raspberry pi with ubuntu. You can use either for communications, but if you've followed
the instructions, you most likely will be using `/dev/serial1`.

Difference between `/dev/serial0` and `/dev/serial1`:
- `/dev/serial0` maps to `/dev/ttyS0`, which handles serial communication through a software "mini-UART" implementation.
- `/dev/serial1` maps to `/dev/ttyAMA0`, which handles serial communication through a hardware PL011 UART implementation.
- The PL011 UART (UART0) is a full-featured universal asynchronous receiver/transmitter for serial communication
- the mini-UART (UART1) has a reduced set of features
- On the RPi4, the PL011 UART is also connected to the bluetooth controller.
<!-- - On the RPi4, the mini-UART is primary, and the PL011 UART is secondary -->

See [this discussion](https://www.engineersgarage.com/microcontroller-projects/articles-raspberry-pi-serial-communication-uart-protocol-serial-linux-devices/) and [this discussion](https://spellfoundry.com/2016/05/29/configuring-gpio-serial-port-raspbian-jessie-including-pi-3-4/) for more information.

- when using `/dev/serial0` for serial communications instead of `/dev/serial1`, you're using a less capable communications device. For whatever reason, this worked under ubuntu 18.04, but but seems to have a lot of trouble under ubuntu 20.04. So it's best to use `/dev/serial1`.
- However, `/dev/serial1` is also connected to the bluetooth controller, so we need to disable bluetooth. This is why we use the `dtoverlay=disable-bt` overlay in config.txt (see [rpi.md](rpi.md))
- We also need to remove `console=serial0,115200` from cmdline.txt, because it also seems to prevent the operation of `serial1` for serial comms.

To find out which one you should be using, run [the test script](../scripts/roboclawtest.py). If you want to use `serial0` instead of `serial1`, you must change
the default in the [config yaml](../osr_bringup/config/roboclaw_params.yaml).

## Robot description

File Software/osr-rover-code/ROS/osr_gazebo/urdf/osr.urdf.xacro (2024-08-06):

<?xml version="1.0" ?>
<robot xmlns:xacro="http://www.ros.org/wiki/xacro" name="rover">
    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

    <xacro:include filename="$(find osr_gazebo)/urdf/gazebo.urdf.xacro"/>
    <xacro:include filename="$(find osr_gazebo)/urdf/insert_transmission.urdf.xacro"/>

    <link name="base_footprint"/>
    <link name="base_link">
        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

	    <inertial>
            <origin rpy="0 0 0" xyz="0 0 0"/>
            <mass value="10"/>
            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
        </inertial>

    </link>

    <joint name="base_joint" type="fixed">
        <parent link="base_footprint"/>
        <origin rpy="0 0 0" xyz="0 0 0.273745"/>
        <child link="base_link"/>
        <axis xyz="0 0 1"/>
    </joint>


    <link name="box_rotate">
        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

        <inertial>
            <origin rpy="0 0 -3.14" xyz="0 0 0"/>
            <mass value="0.2"/>
            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
        </inertial>
    </link>

    <joint name="body_joint" type="fixed">
        <parent link="base_link"/>
        <origin rpy="0 0 0" xyz="-0.071275 0 0.080475"/>
        <child link="box_rotate"/>
        <axis xyz="0 0 1"/>
    </joint>

    <xacro:macro name="arm_rotate" params="prefix dir">
        <link name="arm_rotate_${prefix}">
            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

            <inertial>
                <origin rpy="0 0.2 0" xyz="0 0 0"/>
                <mass value="0.1"/>
                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

            </inertial>
        </link>

        <joint name="arm_rotate_join_${prefix}" type="fixed">
            <parent link="box_rotate"/>
            <origin rpy="0 0.0 0" xyz="0 ${dir*0.153} 0"/>
            <child link="arm_rotate_${prefix}"/>
            <axis xyz="0 1 0"/>
        </joint>
    </xacro:macro>
    <xacro:arm_rotate prefix="L" dir="1"/>
    <xacro:arm_rotate prefix="R" dir="-1"/>

    <xacro:macro name="turn_bukles" params="prefix dir origin">
        <link name="turn_bukles_link_${prefix}">
            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
            <inertial>
                <origin rpy="0 0 0" xyz="0 0 0.0"/>
                <mass value="1"/>
                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
            </inertial>

        </link>

        <joint name="turn_bukles_joint_${prefix}" type="fixed">
            <parent link="arm_rotate_${prefix}"/>
            <origin rpy="0 0 0" xyz="0.071558 ${dir*0.017545} -0.084292"/>
            <child link="turn_bukles_link_${prefix}"/>
            <axis xyz="0 1 0"/>
        </joint>

    </xacro:macro>
    <xacro:turn_bukles prefix="L" dir="1" origin="0"/>
    <xacro:turn_bukles prefix="R" dir="-1" origin ="-1.57"/>

    <xacro:macro name="body_axis_link" params="prefix dir">
        <link name="body_axis_link_${prefix}">
            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
            <inertial>
                <origin rpy="0 0 1.57" xyz="0 0 0.0"/>
                <mass value="0.5"/>
                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
            </inertial>
        </link>

        <joint name="body_axis_joint_${prefix}" type="fixed">
            <parent link="turn_bukles_link_${prefix}"/>
            <origin rpy="0 0 0" xyz="0 ${dir*-0.060920} -0.001245"/>
            <child link="body_axis_link_${prefix}"/>
            <axis xyz="0 1 0"/>
        </joint>

    </xacro:macro>
    <xacro:body_axis_link prefix="L" dir="1"/>
    <xacro:body_axis_link prefix="R" dir="-1"/>

    <xacro:macro name="rocker_bogie_link" params="prefix dir">
        <link name="rocker_bogie_link_${prefix}_1">
            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

            <inertial>
                <origin rpy="0 0 0" xyz="0 0 0.0"/>
                <mass value="7"/>
                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 
            </inertial>

        </link>

        <joint name="rocker_bogie_joint_${prefix}_1" type="fixed">
            <parent link="body_axis_link_${prefix}"/>
            <origin rpy="0 0 0" xyz="0.016004 ${dir*0.071485} 0.001353"/>
            <child link="rocker_bogie_link_${prefix}_1"/>
            <limit effort="10000.0" velocity="0.5" lower="-0.5" upper="0.5"/>
            <axis xyz="0 1 0"/>
        </joint>

        <link name="rocker_bogie_link_${prefix}_2">
            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

            <inertial>
                <origin rpy="0 0 0" xyz="0 0 0.0"/>
                <mass value="3"/>
                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
            </inertial>

        </link>

        <joint name="rocker_bogie_joint_${prefix}_2" type="revolute">
            <parent link="rocker_bogie_link_${prefix}_1"/>
            <origin rpy="0 0 0" xyz="0.099618 0 -0.091275"/>
            <child link="rocker_bogie_link_${prefix}_2"/>
            <limit effort="10000.0" velocity="1.0" lower="-0.5" upper="0.5"/>
            <axis xyz="0 1 0"/>
        </joint>

    </xacro:macro>
    
    <xacro:rocker_bogie_link prefix="L" dir="1"/>
    <xacro:rocker_bogie_link prefix="R" dir="-1"/>

    <xacro:macro name="wheel_link" params="prefix dir origin">
        <link name="front_wheel_link_${prefix}">
            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

            <inertial>
                <origin rpy="0 0 ${dir*-1.57}" xyz="0 0 0.0"/>
                <mass value="0.8"/>
                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
            </inertial>
        </link>

        <joint name="front_wheel_joint_${prefix}" type="revolute"> 
        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
            <parent link="rocker_bogie_link_${prefix}_2"/>
            <origin rpy="0 0 0" xyz="0.170113 -0.000335 0.076721"/>
            <child link="front_wheel_link_${prefix}"/>
            <limit effort="100000.0" velocity="10" lower="-0.523599" upper="0.523599"/>
            <axis xyz="0 0 1"/>
        </joint>

        <link name="middle_wheel_link_${prefix}">
            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

            <inertial>
                <origin rpy="${origin} 0 ${-dir*1.57}" xyz="0 0 0.0"/>
                <mass value="0.3"/>
                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
            </inertial>

        </link>

        <joint name="middle_wheel_joint_${prefix}" type="fixed">
            <parent link="rocker_bogie_link_${prefix}_2"/>
            <origin rpy="0 0 0" xyz="-0.101456 ${dir*0.000053} -0.100276"/>
            <child link="middle_wheel_link_${prefix}"/>

            <axis xyz="0 1 0"/>
        </joint>

        <link name="rear_wheel_link_${prefix}">
            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

            <inertial>
                <origin rpy="0 0 ${-dir*1.57}" xyz="0 0 0.0"/>
                <mass value="0.8"/>
                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

            </inertial>

        </link>

        <joint name="rear_wheel_joint_${prefix}" type="revolute">
        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
            <parent link="rocker_bogie_link_${prefix}_1"/>
            <origin rpy="0 0 0" xyz="-0.311763 0 -0.030379"/>
            <child link="rear_wheel_link_${prefix}"/>
            <limit effort="100000.0" velocity="3" lower="-0.523599" upper="0.523599"/>
            <axis xyz="0 0 1"/>
        </joint>

    </xacro:macro>

    <xacro:wheel_link prefix="L" dir="1" origin="1.57"/>
    <xacro:wheel_link prefix="R" dir="-1" origin="-3.14"/>

    <xacro:macro name="wheel" params="prefix dir origin prefix_1">
        <link name="front_wheel_link_${prefix}">
            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

            <inertial>
                <origin rpy="-1.57 0 ${origin}" xyz="0 0 0.0"/>
                <mass value="0.8"/>
                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
            </inertial>

        </link>

        <joint name="front_wheel_joint_${prefix}" type="continuous">
            <parent link="front_wheel_link_${prefix_1}"/>
            <origin rpy="0 0 0" xyz="0.006231 ${dir*0.019544} -0.169991"/>
            <child link="front_wheel_link_${prefix}"/>
            <axis xyz="0 1 0"/>
            <velocity>5.0</velocity>
        </joint>

        <link name="middle_wheel_link_${prefix}">
            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

            <inertial>
                <origin rpy="-1.57 0 ${origin}" xyz="0 0 0.0"/>
                <mass value="0.8"/>
                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
            </inertial>
        </link>

        <joint name="middle_wheel_joint_${prefix}" type="continuous">
            <parent link="middle_wheel_link_${prefix_1}"/>
            <origin rpy="0 0 0" xyz="0.006691 ${dir*0.100382} 0.005425"/>
            <child link="middle_wheel_link_${prefix}"/>
            <axis xyz="0 1 0"/>
            <velocity>5.0</velocity>
        </joint>

        <link name="rear_wheel_link_${prefix}">
            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

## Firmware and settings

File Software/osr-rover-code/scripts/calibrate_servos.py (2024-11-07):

"""
Simple calibration/test script for PCA9685 PWM motor control

Moves motors back and forth

Setup:
$ pip3 install adafruit-circuitpython-servokit

Instructions: https://learn.adafruit.com/adafruit-16-channel-servo-driver-with-raspberry-pi/using-the-adafruit-library
"""
from time import sleep
import argparse

from adafruit_servokit import ServoKit


if __name__ == '__main__':
    parser = argparse.ArgumentParser(
                        prog='ServoCalibrator',
                        description='Helps calibrate the corner motors. When running this script, make sure that the servo motors can move freely.',
                        epilog='If you need help, please ask on Slack on the #troubleshooting channel!')
    
    parser.add_argument('motor_index', type=int, choices=range(16), help="which channel on the PCA9685 board and thus which motor we're commanding. "
                                                               "Normally, 0 corresponds to the back right corner, 1 to the front right, 2 to the front left, and 3 to the back left.")
    parser.add_argument('target_angle', type=int, help="what angle to send the motor to, should be a value somewhere between 120 and 180.")
    args = parser.parse_args()

    kit = ServoKit(channels=16)
    sleep(0.1)
    kit.servo[args.motor_index].actuation_range = 180
    kit.servo[args.motor_index].set_pulse_width_range(375, 1800)
    kit.servo[args.motor_index].angle = args.target_angle
    print(f"Servo motor at channel {args.motor_index} was set to {args.target_angle}")

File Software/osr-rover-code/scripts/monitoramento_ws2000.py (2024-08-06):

import os
import time
import rclpy
from rclpy.node import Node
from sensor_msgs.msg import Joy
from evdev import InputDevice, ecodes

SERIAL_PORT = '/dev/input/event0'  # Substitua pelo dispositivo serial correto
CHECK_INTERVAL = 0.5  # Intervalo de checagem em segundos
TIMEOUT_INTERVAL = 2  # Tempo máximo sem eventos antes de considerar desconexão

class JoyPublisher(Node):
    def __init__(self):
        super().__init__('joy_publisher')
        self.publisher_ = self.create_publisher(Joy, 'joy', 10)
        self.timer = self.create_timer(CHECK_INTERVAL, self.timer_callback)
        self.joy_msg = Joy()
        self.joy_msg.axes = [0.0] * 8
        self.joy_msg.buttons = [0] * 12
        self.last_button_release_time = None  # Nova variável para rastrear o tempo de liberação do botão

        self.device = self.connect_device(SERIAL_PORT)

    def connect_device(self, serial_port):
        try:
            device = InputDevice(serial_port)
            self.get_logger().info(f"Conectado ao dispositivo: {serial_port}")
            return device
        except PermissionError as e:
            self.get_logger().error(f"Permissão negada para acessar {serial_port}: {e}")
            raise
        except FileNotFoundError as e:
            self.get_logger().error(f"Dispositivo não encontrado: {serial_port}: {e}")
            raise

    def timer_callback(self):
        current_time = time.time()
        if self.last_button_release_time:
            time_diff = current_time - self.last_button_release_time
            self.get_logger().info(f'Current time: {current_time}, Last button release time: {self.last_button_release_time}, Time difference: {time_diff}')
            if time_diff > TIMEOUT_INTERVAL:
                self.get_logger().info('Nenhum evento detectado em 5 segundos após soltar o botão, zerando eixos e botões...')
                self.reset_joy_msg()
                self.publisher_.publish(self.joy_msg)
                self.reboot_system()

    def reset_joy_msg(self):
        self.joy_msg.axes = [0.0] * 8
        self.joy_msg.buttons = [0] * 12

    def reboot_system(self):
        self.get_logger().info('Reiniciando o sistema...')
        os.system('reboot')

    def run(self):
        while rclpy.ok():
            try:
                for event in self.device.read_loop():
                    if event.type == ecodes.EV_KEY and event.code == 304:
                        self.get_logger().info(f"Botão {event.code}: {event.value}")
                        if event.value == 0:  # Botão foi liberado
                            self.last_button_release_time = time.time()
                            self.get_logger().info(f"Botão 304 liberado: {self.last_button_release_time}")
                        else:  # Botão foi pressionado
                            self.last_button_release_time = None  # Reseta o tempo de liberação
                        self.publisher_.publish(self.joy_msg)
                    time.sleep(0.01)
            except Exception as e:
                self.get_logger().error(f"Erro ao ler evento: {e}")

def main(args=None):
    rclpy.init(args=args)
    joy_publisher = JoyPublisher()
    executor = rclpy.executors.MultiThreadedExecutor()
    executor.add_node(joy_publisher)
    try:
        joy_publisher.run()
    except KeyboardInterrupt:
        pass
    joy_publisher.destroy_node()
    rclpy.shutdown()

if __name__ == '__main__':
    main()

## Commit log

2024-08-06 Port from last team
    [base.dxf, base.f3d, buraco_superior.dxf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]
2024-08-16 change Twist processing for in-place rotation using yaw
2024-08-16 Enable wheel odometry
2024-08-25 RtabMap launch - add commented options for tests with 2D lidar
2024-09-03 RTAB-MAP launch: imu + rgbd sync options
2024-09-14 Launch updates: imu and tf
2024-09-23 removed jetson
2024-09-30 IR depth + imu
2024-10-29 revert osr control parameters
    [rover.py, servo_control.py]
2024-11-06 CAD models - autonomous base dxf/prt
    [caixa.prt, laterais.dxf, laterais.prt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]
2024-11-06 sphinx acrylic case
2024-11-07 Fix servo range
2024-11-23 nmea gps driver
2024-11-24 Updated docs
    [suporte_camera_base.f3d, suporte_camera_fixador.f3d, suporte_lidar.f3d]
2024-11-25 lidar working
